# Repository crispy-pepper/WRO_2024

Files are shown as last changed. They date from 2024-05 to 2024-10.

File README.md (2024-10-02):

# SJJ | WRO - Future Engineers | Canada

## Team Members 
- Sunni Xue (right)
- Jayden Li (middle)
- John Weng (left) <br>
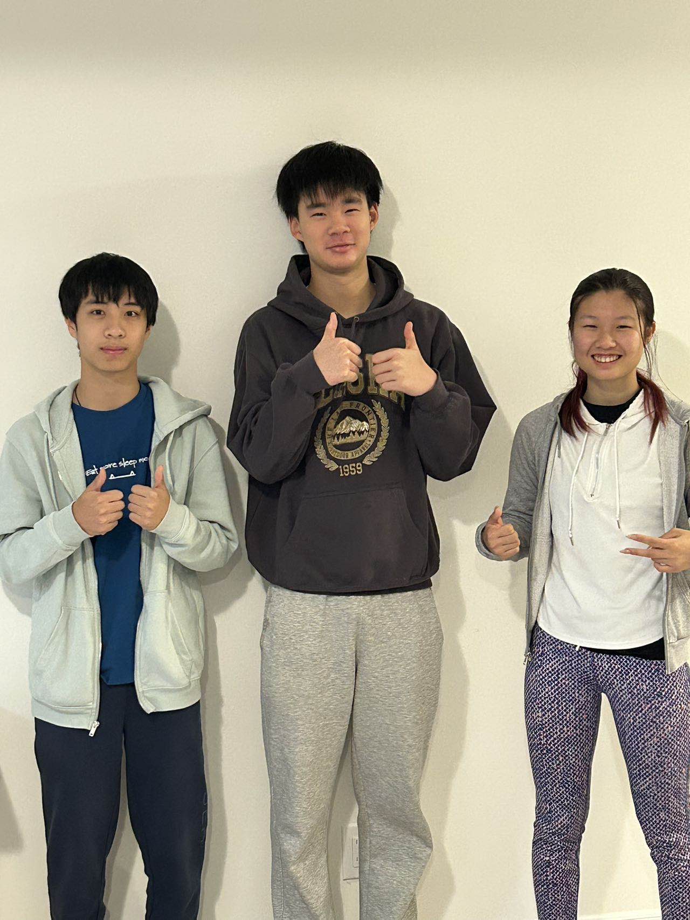
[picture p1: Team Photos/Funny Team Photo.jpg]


## Content 📖📚
 
| Folder  | Content| 
| -- | -- |
| [`Team Photos`](/Team%20Photos)| [Official team photo](/Team%20Photos/Official%20Team%20Photo.jpg), [funny team photo](/Team%20Photos/Funny%20Team%20Photo.jpg) |
| [`Vehicle Photos`](/Vehicle%20Photos) | [Bottom view](/Vehicle%20Photos/bottom.jpg), [front view](/Vehicle%20Photos/front.jpg), [left view](/Vehicle%20Photos/left.jpg), [rear view](/Vehicle%20Photos/rear.jpg), [right view](/Vehicle%20Photos/right.jpg), [top view](/Vehicle%20Photos/top.jpg) |
| [`models`](/models) | [Final base model](/models/base%20v3.stl), [final camera base model](/models/camera%20base.stl), [final camera holder model](/models/camera%20holder%20v5.stl), [expansion board diagram](/models/expansion_board_diagram.png), [final fan holder model](/models/fan%20holder%20v2.stl), [old and unused models (zipped)](/models/old) |
| [`other`](/other) | [Images used in documentation](other/images-used) |
| [`schemes`](/schemes) | [Schematic explanations](/scheme/README.md), [expansion board schematic](/schemes/Raspberry%20Pi%20Expansion%20Board%20Schematic.png), [Raspberry Pi schematic](/schemes/Raspberry%20Pi%20Schematic.png), [vehicle schematic](/schemes/Vehicle%20Schematic.png) |
| [`src`](/src) | [Obstacle challenge final](/src/ObstacleChallenge.py), [open challenge final](/src/OpenChallengeFinal.py), [HSV finder](/src/HSVRange.py), [test files](/src/Tests) |
| [`videos`](/videos) | [Open challenge](/video/README.md), [obstacle challenge](/video/README.md) |

Section  | Content 
--- | --- |
[`Task`](#task) | Introduces the problem/task of this competition
[`Engineering Materials`](#engineering-materials) | Engineering materials used to complete the vehicle 
[`Obstacle Management`](#obstacle-management) | Obstacle Management
[`Movement Considerations`](#movement-considerations) | How and why we chose the specific moving parts used in the vehicle
[`Power Considerations`](#power-considerations) | How and why we chose the battery used with the vehicle
[`Assembly Instructions`](#assembly-instructions) | How to build the vehicle

## Task
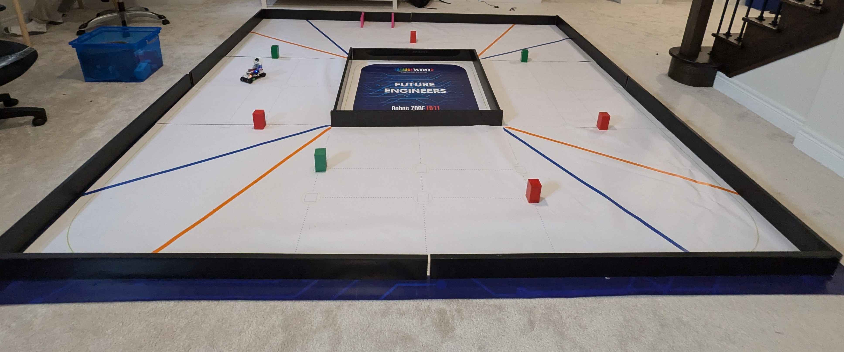
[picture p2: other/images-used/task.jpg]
plot

Obstacle challenge field

### Problem Statement
[The self-driving car challenge in this season is a Time Attack race: there will not be multiple cars at the same time on the track. Instead, one car per attempt will try to achieve the best time by driving several laps fully autonomously. The traffic signs indicate the side of the lane the vehicle has to follow.](https://www.wro2022.org/theme/future-engineers)

In order to perform the race, the car must drive three laps. The vehicle is not allowed to move or knock down the traffic signs.

**GOAL: Build a self-driving, autonomous vehicle that completes 2 challenges: the open challenge and the obstacle challenge.** 
### Open Challenge
The open challenge is where the car must complete three full laps around the field without touching a wall. The size of each side of the field is determined by random chance of either 100 cm or 60 cm. The direction in which the car drives is also randomized. 
 
### Obstacle Challenge
The obstacle challenge is where the car must complete three full laps around the field, avoiding different coloured traffic signs (pillars). If the pillar is red, traverse on the right side; if the pillar is green, traverse on the left. The direction in which the car drives is randomized. After the third lap, depending on the last pillar, the car must continue in the same direction or change directions to find the parking lot. The car must then back into the parking lot without touching either of the ends. The size of each side of the field remains constant, 1 metre for each side. 

## Engineering materials
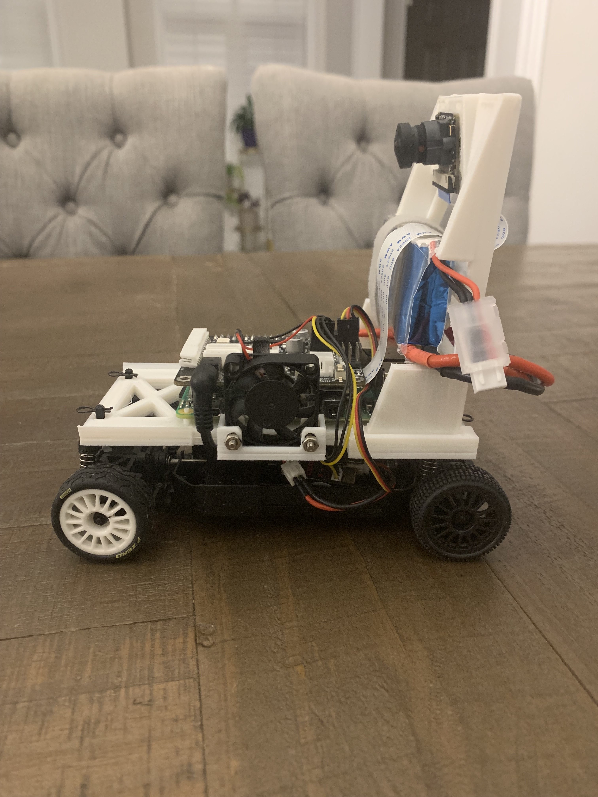
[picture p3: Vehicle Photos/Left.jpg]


### Car Base
* [Carisma 80468 GT24RS 1/24 4WD On-Road Brushless RTR Retro Rally Car as the structure](https://www.ebay.ca/itm/134622499234)
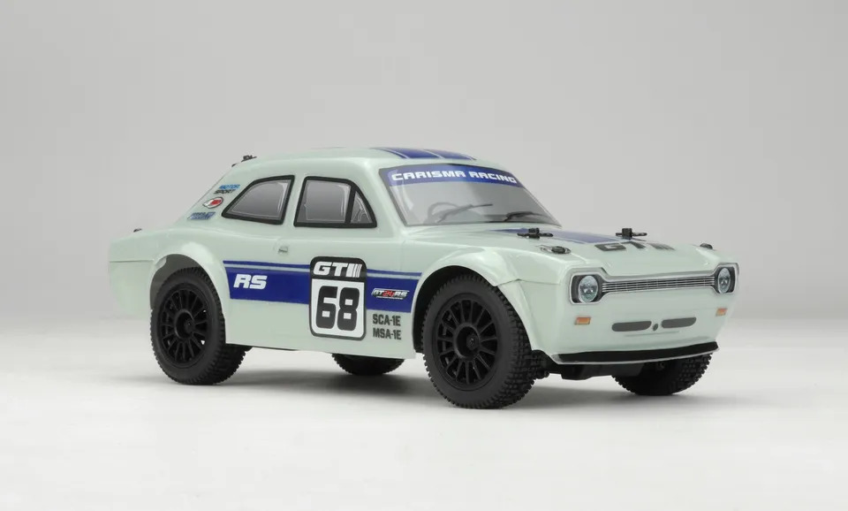
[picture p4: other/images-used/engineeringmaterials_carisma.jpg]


* Carisma 2022 Ford PUMA Hybrid Rally 1 M-Sport 4WD 1/24 Scale RTR 1 87868 as steering system of the car
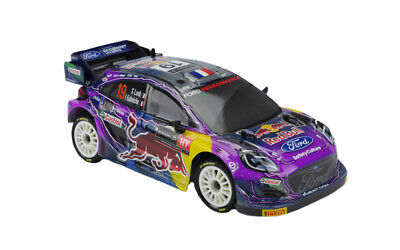
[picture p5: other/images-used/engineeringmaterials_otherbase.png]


* [Furitek Micro Komodo 1212 3450KV Brushless Motor](https://furitek.com/products/furitek-micro-komodo-1212-3456kv-brushless-motor-with-15t-steel-pinion-for-fury-wagon-fx118)
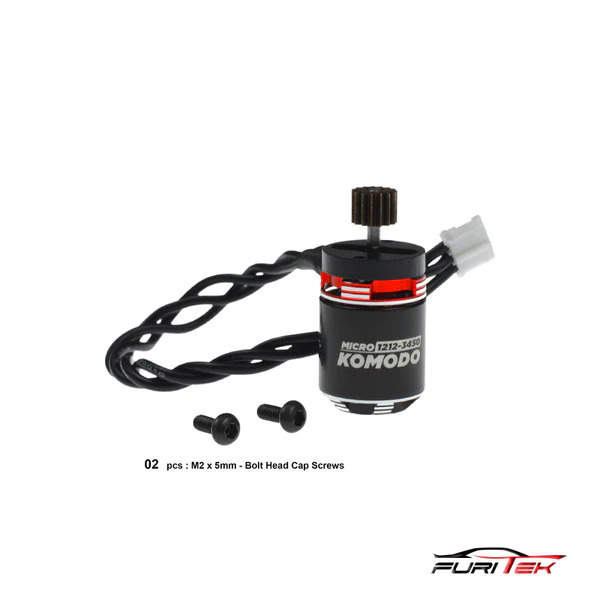
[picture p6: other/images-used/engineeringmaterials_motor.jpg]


* [Furiteck Lizard Pro 30A/50A Brushless ESC](https://furitek.com/products/combo-of-furitek-lizard-pro-30a-50a-brushed-brushless-esc-for-axial-scx24-with-bluetooth)
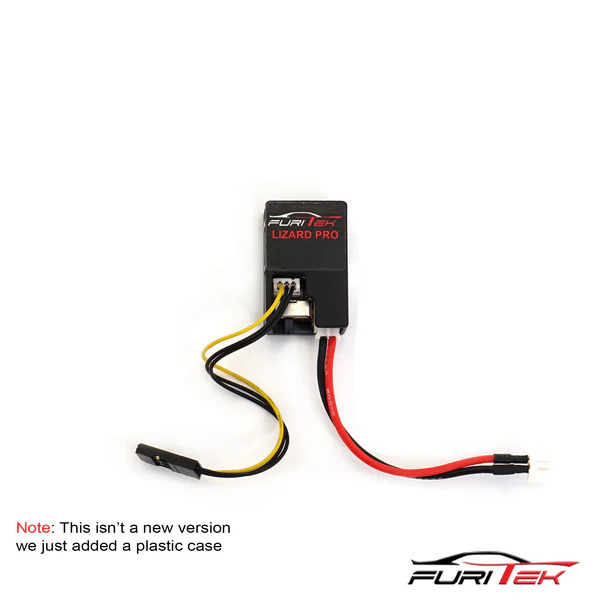
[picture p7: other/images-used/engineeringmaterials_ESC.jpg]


* [Hitec HS-5055MG Servo](https://ca.robotshop.com/products/hs-5055mg-metal-gear-micro-servo-motor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)
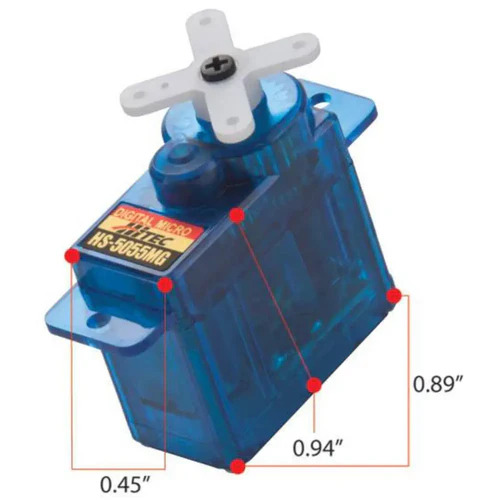
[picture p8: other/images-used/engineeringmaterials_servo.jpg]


* [Gens Ace 2S1P 1300mAh 7.4V battery](https://www.adrenalinehobby.com/products/gens-ace-g-tech-1300mah-2s-7-4v-25c-lipo-deans-plug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)
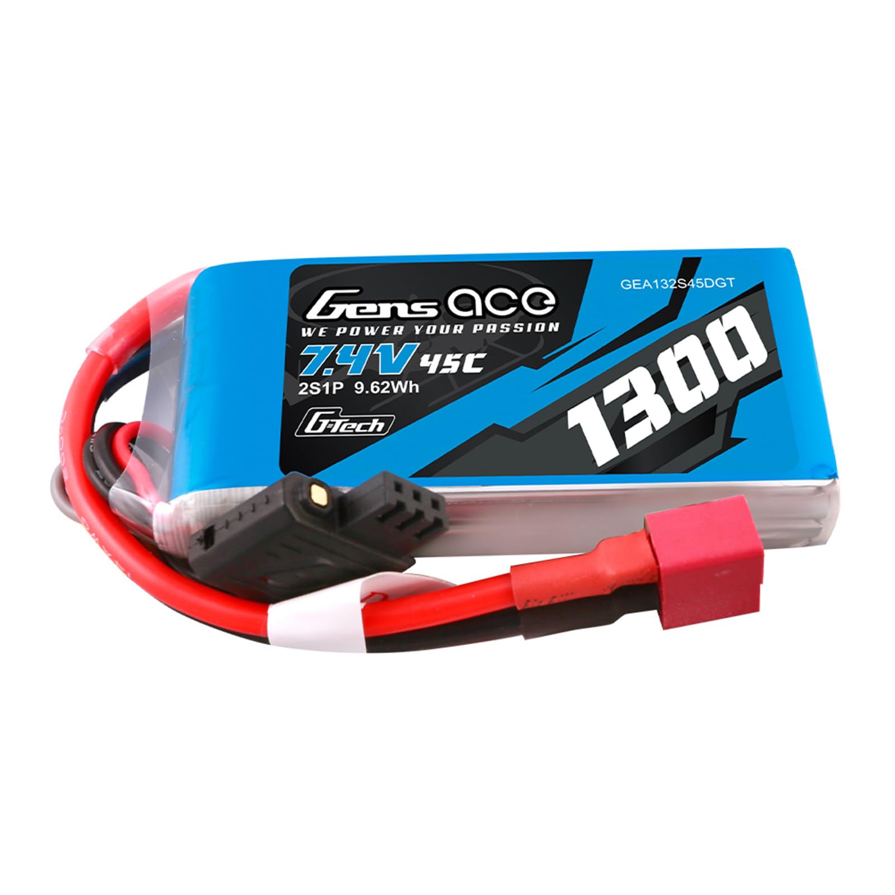
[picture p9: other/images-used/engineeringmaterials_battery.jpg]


* Rasberry PI 4 Model B
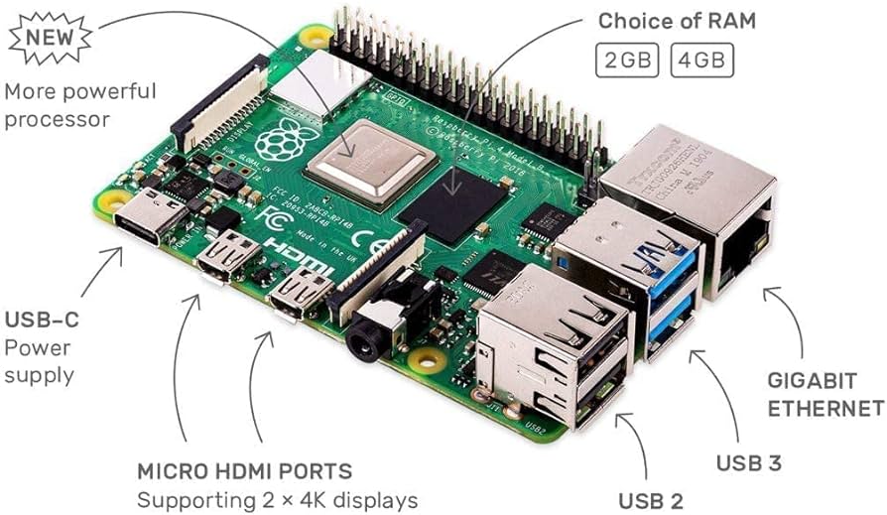
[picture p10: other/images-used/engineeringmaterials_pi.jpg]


* [Raspberry Pi 5 Expansion Board Model A(DC Port)](https://www.hiwonder.com/collections/expansion-board/products/expansion-board-for-raspberry-pi-5)

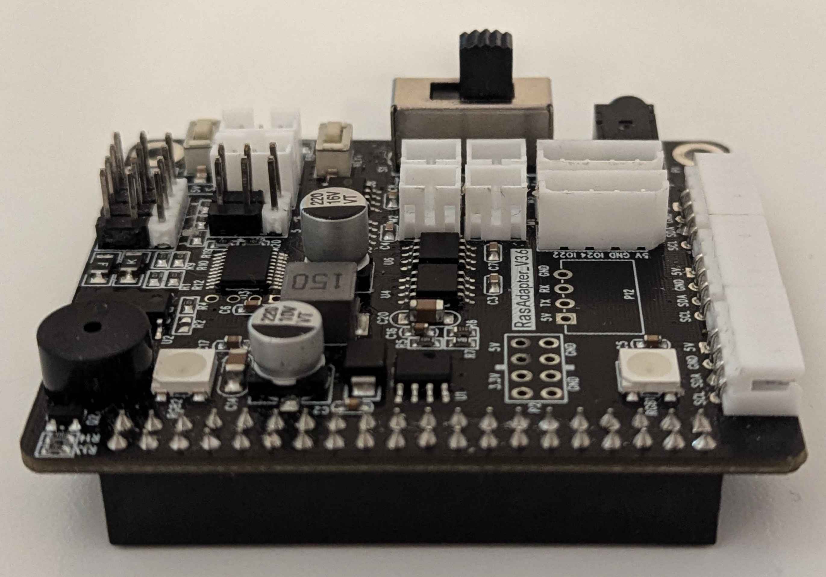
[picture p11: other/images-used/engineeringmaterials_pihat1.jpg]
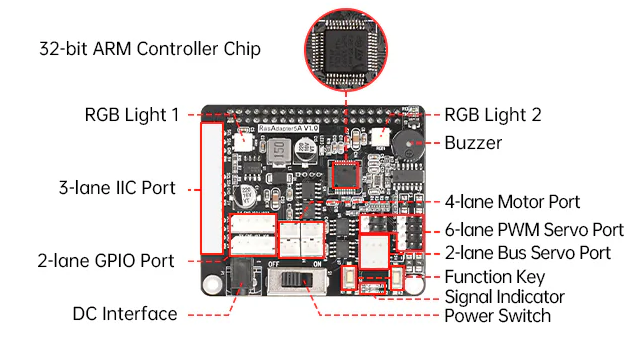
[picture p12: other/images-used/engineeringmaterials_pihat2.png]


* Mini Rocker Switch
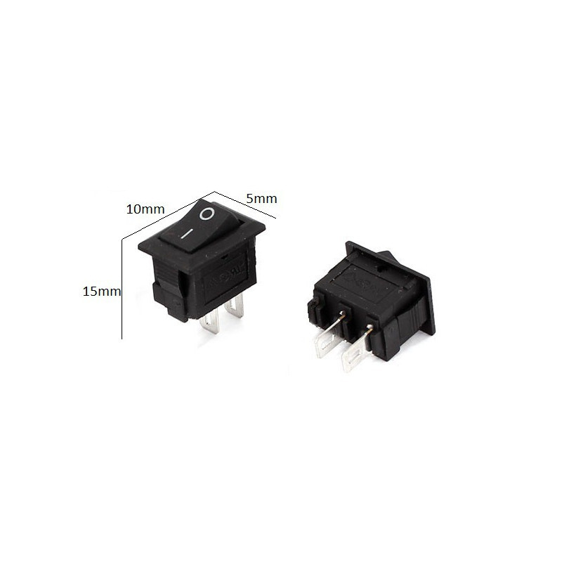
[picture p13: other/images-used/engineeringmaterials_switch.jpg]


* 5V Mini Fan
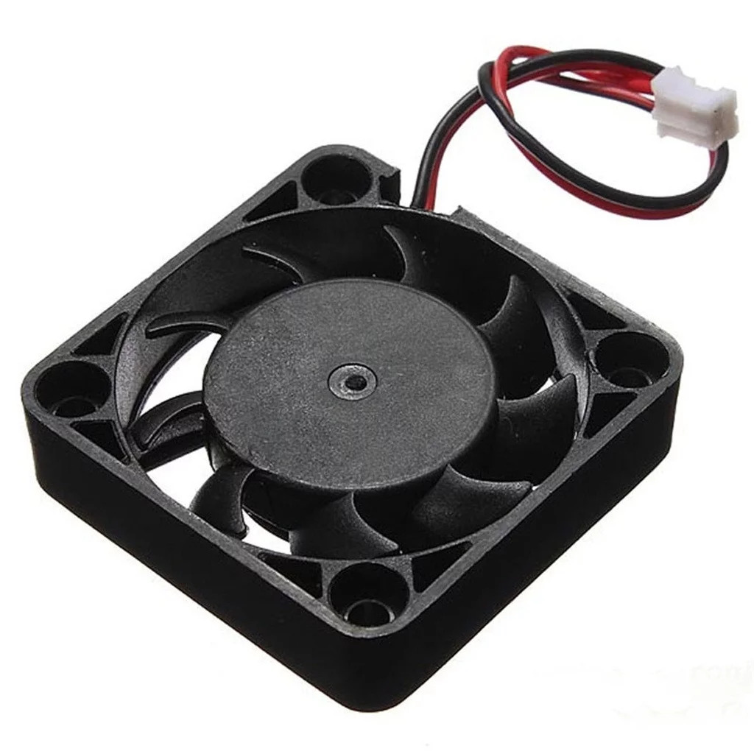
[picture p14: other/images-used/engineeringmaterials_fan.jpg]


* [3D printed base](/models)
* MicroSD card

### Sensors

* [SainSmart Camera Module RPi3, 5MP, Fish-Eye](https://www.sainsmart.com/products/noir-wide-angle-fov160-5-megapixel-camera-module)
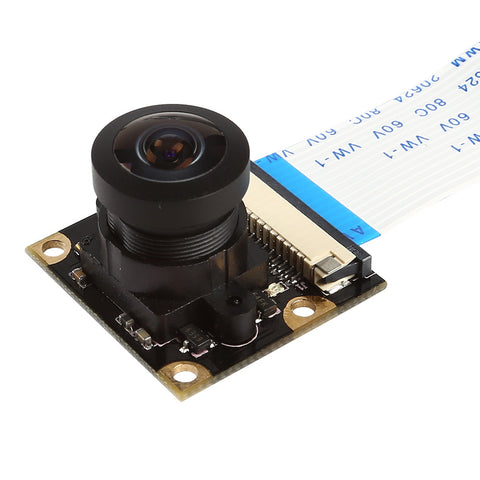
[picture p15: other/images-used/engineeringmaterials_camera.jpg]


## Obstacle Management
**ss of cv2 window**

- **Libraries Used** - `math` - `sys` - `cv2` - `numpy` - `time` - `picamera2` - `HiwonderSDK.Board` - `libcamera`

#### Wall-Following/Track Centering

Our open and obstacle challenge used the same wall following algorithm that guaranteed the robot to remain in the center of the two walls when needed. To make sure that laps stayed consistent and the vehicle did not touch the walls, we had to implement some form of track centering. We did this using a [SainSmart Camera Module RPi3, 5MP, Fish-Eye](#engineering-materials). With the mounted camera, we were able to capture the surroundings of the vehicle frame by frame. 

Using these captures, we applied four (left top, left bottom, right top, right bottom) unique ROIs (regions of interest) that captured the areas of the walls diagonally ahead on both sides. We then created a black threshold mask to calculate how much area of the ROIs was black. Using these areas, we could determine if the vehicle is veering too far to one side by calculating the difference between the two sides and adjust the robot accordingly. To physically implement this calculation, we used a Proportional-Derivative (PD) algorithm approach, deciding that a combining the two factors would be perfect for our goal of following the walls.

```py
error = left_area - right_area
turn (error)(proportional gain) + (change in error value over time)(derivative gain)
```

This algorithm calculates the precise angle the servo should turn by taking the difference between the two sides multiplied it by the proportional value (constant) and adding it to the derivative value (constant) multiplied by the difference between the current and last difference in the two sides. The use of PID control allows stable turning with less oscillating and overcorrection, ensuring that the vehicle remains centered on the track.

### Open Challenge

#### Turning
Our initial turning algorithm was simple in premise: when one of the walls was no longer detected, the robot would turn that direction. In practice, this algorithm performed inadequately because when turning into a narrow section, the robot would not turn at a great enough angle and therefore veer too close to the wall.

```py
if left_area is none
	turn sharp left until left_area is detected
else if right_area is none
	turn sharp right until right_area is detected
```

Realizing that waiting for the wall to be passed would not provide an adequate turn, our goal was to create a turn algorithm that could pre-emptively detect that a turn was needed. Our solution was to use the blue and orange lines on the mat to decide when to turn. Another small ROI was added to detect orange and blue contours. 

Depending on which of the colours was detected first, the algorithm would turn the correct direction accordingly. The turn would be ended after the opposite colour line was detected and the respective wall was detected again on the camera.

The same logic for if a wall was no longer detected from the first algorithm was also used in conjunction, creating an algorithm that would turn in a more optimized path. 

```py
if orange line detected
	turn sharp right until blue line detected
	
else if blue line detected
	turn sharp left until orange line detected
	
if left_area is none
	turn sharp left until left_area is detected
else if right_area is none
	turn sharp right until right_area is detected
```

This algorithm performed much better, but had a flaw: the line would be detected and the turn would start, but once the orange line was detected again, the turn would end. Therefore, we created a solution that would allow for the wall to fully be passed before ending the turn. This solution was adding a short timer to the turn that would ensure that the turn was not ended early.

```py
if orange line detected
	turn sharp right until blue line detected
	
	if blue line detected
		increment turn_timer
		
	if turn_timer greater than turn time
		end the turn
	
else if blue line detected
	turn sharp left until orange line detected
	
	if orange line detected
		increment turn_timer
	
	if turn_timer greater than turn time
		end the turn
		
if left_area is none
	turn sharp left until left_area is detected
	
else if right_area is none
	turn sharp right until right_area is detected
```

This algorithm was both reliable and efficient, allowing the robot to travel at high speeds with no risk of hitting the walls. 

### Obstacle Challenge

#### Turning
Similar to how we centered the vehicle, we also used the area of black in the ROIs to decide when to turn. If one ROI's black area was less than a certain value, it would mean that the wall has disappeared and the servo would turn to the most extreme angle. The vehicle would keep turning until the wall appeared again. This naïve approach was straightforward but failed in many cases because of the pillar-avoidance requirement:

```py
if left_area is none
	turn sharp left until left_area is detected
else if right_area is none
	turn sharp right until right_area is detected
```

However, this did not always work because pillars would make the robot move into unexpected areas. To fix this, we added another trigger for the turning sequence: the lines on the mat. This algorithm was very similar to the line detection in the open challenge without the timed aspect later added to that algorithm. 

```py
if orange line detected
	turn sharp right until blue line detected
	if right_area is detected
		stop turning
	
if blue line detected
	turn sharp left until orange line detected
	if left area is detected 
		stop turning
```

If a pillar was detected in the turn, the turn would be ended when the pillar is on the correct side of the screen. For example, when turning left into a green pillar, the turn would be ended when the green pillar is on the right side of the screen. This ensures that the turn allows the robot to travel into the next straight section while passing pillars on the correct side. 

#### Pillar Maneuvering

The camera scans for pillars using another ROI that encapsulates the center of the camera view and a red and green colour mask. The algorithm would find the closest pillar by finding the largest contour. Depending on the colour of this contour, we could decide whether to go left or right. We started with a naïve approach of turning a constant amount left or right when the pillar was detected.

##### Pillar Maneuvering: 
The camera scans for pillars using another ROI that encapsulates the center of the camera view and a red and green colour mask. The algorithm would find the closest pillar by finding the largest contour. Depending on the colour of this contour, we could decide whether to go left or right. We started with a naïve approach of turning a constant amount left or right when the pillar was detected.

```py
if red_area greater than pillar_threshold
	turn right
else if green_area greater than pillar_threshold
	turn left
```

However, this posed many challenges with overturning, underturning, turning past before it got to the pillar, and not turning at all. We fixed this by adding a constant target value for both coloured pillars and adjusting according to the distance between the pillar's left x-value and the target line. The vehicle would constantly try to match the x-value up with the target line. This way, the vehicle would know to continue turning towards the pillar or to turn the other way to correct the overturning. Additionally, we found that it would be beneficial for the robot to turn at a greater angle if the pillar is closer to avoid the pillar in urgent situations. Therefore, we added another factor into our turn degree: y-axis gain. This functionality would turn the servo motor at a greater angle based on the y-coordinate of the pillar, which is the straight distance forward from the robot. 

```py
if red_area greater than pillar_threshold
	error = target - red_pillar_x
	turn (error)(pillar proportional gain) 
	+ (change in error value over time)(pillar derivative gain)
	+ (y axis gain)(red_pillar_y)
	
```

#### Backtracking: 
Because there was a limitation to how many degrees our vehicle could turn at a time, there was an issue of not turning enough in time. To solve this, we would check how big the current pillar was and calculate if the vehicle would make it past successfully (without touching or moving anything). If the vehicle could not, it would backtrack at the opposite angle, readjust, and continue forward. This would continue until the vehicle could successfully make it past.

```py
if pillar_area greater than avoidable distance and pillar_x is not on the correct side:
	reverse the robot
```

#### 3-Point Turn

The three point turn algorithm is required when the last pillar of the second lap is red. This signals that the robot must complete the final lap in the opposite direction. A three point turn is required to change the orientation of the robot. The algorithm is simple and effective. If the three point turn is needed, the robot will turn sharply right until a wall is seen. This allows the robot to achieve the maximum angle from one turn. Once a wall is detected in front of the robot, the second phase of the turn will be activated and the servo will turn to a sharp left angle and reverse the robot. Finally, the robot turns at a sharp right angle and goes forward, ending in the opposite orientation from where it started. This allows the robot to complete the last lap in the appropriate direction.

```py
three point turn
	turn sharp right 
	go forward
	if wall is directly in front of robot
		turn sharp left
		reverse the robot
		turn sharp right
		go forward
		end the three point turn
	repeat
		
if last pillar is red
	go past the pillar
	start three point turn
```

#### Parking
After finishing the three laps, the vehicle must park find and stop inside the magenta parking lot. Rather than parallel parking, we decided to go head first, directly turning into the allotted space. This was because when first reading the problem, we found that as long as the vehicle was fully inside the boundaries of the parking lot, the orientation did not matter to achieve full marks. This is also the main driving factor behind why we chose a small chassis (< 20 cm because the width of the parking lot is 20 cm).

The parking algorithm works by first circling the field on the outside of all pillars (as it does not need to abide by the traffic rules after the completion of the third lap) until it detects a large enough magenta contour to initiate the parking sequence. This condition is calculated by finding the largest magenta contour in the left and right ROIs and the y-coordinates of their bounding rectangles and comparing them to predetermined constants. If both the y-coordinate and size conditions are met, the vehicle is in the correct position to start parking. Depending on the size of the maximum left and right magenta contour, the side the parking lot is located on can be deduced. 

```py
if rightY/leftY is greater than a value and maxAreaRight/maxAreaLeft is greater than a value
	if not currently parking on the left or right side:
		initiate parking on the left/right side
		go forwards slower
                created new, bigger center ROI
```

The parking sequence works by directly turning into the parking lot forward and backing out in the same direction if needed; repeated until the area in front of the vehicle is larger than a value. It knows when to back out by checking if the center y-coordinate of the largest contour's bounding rectangle (centerY) is greater than a certain, meaning the vehicle will hit the wall if it continues forward.

```py
if currently parking on the left or right side
	if centerY is greater than a value:
		stop
		turn the servo to the maximum in the correct direction
		go backwards
		stop

	else
		turn the servo to the maximum in the correct direction
		go forwards
```

Once the area of the wall in front of the vehicle is large enough, it will continue straight forward to be sure the vehicle is fully in, stop, and exit the main loop.

```py
 if area in front is greater than a value:
	turn servo straight
	go forwards
	stop and exit
```

## Movement Considerations
* Servo for steering
* Motor for FWD (four-wheel drive)
* The vehicle [Chassis is a Carisma 80468 GT24RS 1/24](#engineering-materials) so the vehicle is small enough to fit in the parallel parking space vertically
* The components are mounted on a 3d printed base sitting on top of the chassis, with the motor and servo being mounted directly into the chassis
* The [Furitek Micro Komodo 1212 3450KV Brushless Motor](#engineering-materials) was chosen combined with a [Furiteck Lizard Pro 30A/50A Brushless ESC](#engineering-materials) because brushless motors are mechanically driven, which allows more precise speed controls, longer life and higher efficiency with less maintenance.
* The servo was chosen because.. (use engineering principles: speed, torque, power etc) <br>


In both the open and obstacle challenge, vehicle movement is essential for ensuring optimal performance. The vehicle is managed through a four-wheel drive configuration, with front-wheel steering. This configuration resembles everyday cars on the street, and allows for movement forwards and backwards, as well as turning in both directions. 

For the propulsion of the vehicle, we choose the [Furitek Micro Komodo 1212 3450KV Brushless Motor](#engineering-materials) due to the high speeds that the motor can achieve, indicated by the 3450KV rating. High speeds allow rapid movements and give us headroom without needing to max out the motor while running. Brushless motors are known for providing consistent torque which allows the vehicle to move smoothly. Brushless motors are electrically driven, which allows more precise speed control, and have a longer lifespan with less maintenance, which is ideal for our vehicle. We paired the motor with a [Furiteck Lizard Pro 30A/50A Brushless ESC](#engineering-materials), which regulates the power delivered to the motor, allowing for smooth acceleration and deceleration and ensures the safety and consistency of the motor.

We chose the [Hitec HS-5055MG Servo](#engineering-materials) for our steering capabilities. It is perfect for small vehicles, with high torque at 1.2kg/cm at 4.8V or 1.5kg/cm at 6V. This allows the turning capabilities of the car to be consistent due to the strength of the servo and ensures the vehicle can turn quickly and accurately at low speeds or when stationary, which is essential for this competition. 

The vehicle is based on the [Charisma 80468 GT24RS 1/24 model](#engineering-materials), which was selected due to its compact size, which allows the vehicle to parallel park vertically, making the job much easier. The small size also contributes to the overall agility of the vehicle, making it easier to maneuver in tight spaces. 

The motor and servo replace the original components in the [Charisma 80468 GT24RS 1/24 model](#engineering-materials), with the servo needing modifications to the chassis of the car. The other components of the car are attached through a 3d printed base that is clipped in on top of the car. <br>

However, our chassis still had one major problem; the max turning degree of the front-wheel steering was less than 30 degrees. This became a major issue later on as with such a large turning radius, the vehicle could not possibly move agilely in difficult pillar configurations. After WRO Canada, we switched out the front-wheel steering area for a different chassis’s front-wheel steering. This new steering piece came from the [Carisma 87868 Ford PUMA Hybrid Rally 1/14](#engineering-materials) This was because we found that through testing, a different front-wheel steering part paired with the same base chassis would result in a higher max turn degree.

## Power Considerations
* Sensors and power management
* Reference schematic 


The power and sensor systems are critical to the vehicle's performance in navigating the challenges of the competition. For this project, the vehicle is powered by a [Gens Ace 2S1P 1300mAh 7.4V battery](#engineering-materials). This battery has a discharge rating of 45C, meaning it can provide up to 58.5 Amps of current, which is more than enough to meet the power requirement of the vehicle's components.

The battery serves as the power source for the vehicle, providing energy for all parts. The [Furitek Lizard Pro 30A/50A Brushless ESC](#engineering-materials) is connected to the battery to regulate the power delivered to the [Furitek Micro Komodo 1212 3450KV Brushless Motor](#engineering-materials). This ESC is required to ensure smooth acceleration and deceleration, protecting the motor from potential damage due to power surges.

The Raspberry Pi, which acts as the vehicle's brain, has a power consumption of 1280mA under heavy stress, shown by studies. Given the battery's capabilities, this power draw is much less than what the battery can provide, allowing the Raspberry Pi to operate properly while managing all sensor inputs and processing.

The vehicle's sensing capabilities include a [SainSmart Camera Module RPi3](#engineering-materials), which is used in both the open and obstacle challenges. The camera is equipped with a fish-eye lens, offering a wider field of view. This visual range enables the vehicle to detect obstacles, such as walls and pillars, and to more effectively process the surroundings. 

In the obstacle challenge, the camera detects the walls, the colour of the pillars, the parking space, and the lines on the course. The vehicle uses this information to change the direction left or right accordingly, ensuring it stays on course. The fish-eye lens enhances the vehicle’s ability to capture more of the field at closer distances, providing the system with more information to make timely decisions.

<br><br><br>

## Assembly Instructions
### Software
**1. Raspberry Pi OS**
 - Download and install the official Raspberry Pi Imager from [https://www.raspberrypi.com/software/]

**2. Turbo Pi**
 - Using Raspberry Pi Imager, copy the TurboPi operating system onto a microSD card
 - Insert into the Raspberry Pi
   
**3. Connecting to the Raspberry Pi**
   - Download and install RealVNC from [https://www.realvnc.com/en/connect/download/viewer/]
   - Plug in the Raspberry and wait until wifi access point “HW-xxxxxx” shows up in your wifi list
   - Launch RealVNC and create a new connection with server `192.168.149.1`
       - Username: pi
       - Password: raspberry
   - 
**3. Auto-running the program on start**
  - Transfer OpenChallengeFinal.py/ObstacleChallengeFinal.py onto the Raspberry Pi and open command prompt
  - Open command prompt and run `sudo nano /etc/rc.local`
  - Add the line `sudo bash -c 'sudo python3 /home/pi/<<directory>>/<<filename.py>>' &` before the line `exit 0` and save and close
  - Reboot the Raspberry Pi and the program should automatically run on start
   
<br><br>
### Hardware
**1. Disassembling the Chassis:**
 - Begin by unscrewing the cover of the Carisma 80468 GT24RS 1/24 chassis. This includes removing the top pole that supports the rear of the cover.
 - Next, unscrew the top shell of the vehicle. After the shell is removed, detach the components securing the servo and motor in place.

**2. Creating Space for New Components:**
 - Remove the battery holder from the chassis, followed by the front partition of the servo holder. This step creates sufficient space for the 
installation of the new motor and servo.

**3. Installing the New Motor:**
 - Replace the original motor with the Furitek Micro Komodo 1212 3450KV Brushless Motor, using the original motor compartment and holder.

**4. Installing the New Servo:**
 - Replace the original servo with the Hitec HS-5055MG Servo. Screw a long screw into the servo horn/arm so that it moves the steering mechanism. 
 - Make sure to clip the standoffs of the servo to fit into the chassis.

**5. Wiring the Power System:**
 - Connect the Gens Ace 2S1P 1300mAh 7.4V battery cable to the Furiteck Lizard Pro 30A/50A Brushless ESC cable. To ensure proper power delivery to the motor and other components, follow the wiring provided in the [README](/schemes/README.md) of the schemes folder

**6. 3D Printed Components Installation:**
 - Print a [base](/models/base%20v3.stl) and a [camera holder](/models/camera%20holder%20v6.stl) using a 3D printer.
 - Install the camera holder into the base by aligning it with the inset negatives on the base.
 - Mount the assembled base onto the poles that originally supported the vehicle’s cover, ensuring the camera holder is positioned over the rear wheels. Use the original pins from the car to securely clip the base in place.

**7. Installing the Camera:**
 - Secure the camera into the holder using screws, aligning it with the holes in the camera holder. Ensure the camera is firmly fixed to prevent any movement during operation.

**8. Mounting the Battery:**
 - Place the battery into the  cutout within the camera holder's supports. Use tape, Velcro, or zip ties to secure the battery in place, ensuring it remains stable during vehicle operation.

**9. Installing the Raspberry Pi:**
 - Place the Raspberry Pi on top of the base, ensuring that the pins on the base align with the screw holes on the Raspberry Pi.

**10. Wiring the Vehicle:**
 - Wire the car together according to the provided schematic, ensuring all connections are secure and correctly aligned. Pay attention to wire management to prevent tangling or obstruction of moving parts or obstruction of the camera.

**11. Final Checks:**
 - Ensure all components are secure and that there is no excess movement. Double-check all wiring connections for correctness and stability.

**12. Running the Code:**
 - Once the assembly is complete, upload the control code to the Raspberry Pi. Check all systems are working by performing a series of tests that can be found in the tests folder located in the src folder.

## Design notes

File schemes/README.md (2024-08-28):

# Electromechanical diagrams

Our vehicle's schematic can be separated into 3 main areas: the power area, [the Raspberry Pi] area(#engineering-materials), and the [Pi expansion board] area(#engineering-materials). <br><br>
****As the Raspberry Pi and expansion board are not of our design, you can find their documentation on their respective sites**
<br>

## The Power Area
The power area contains the [main switch](#engineering-materials), [motor](#engineering-materials) and [motor ESC](#engineering-materials), and [battery](#engineering-materials).  Mandated by the rules, the main switch controls all power flowing through the vehicle. The switch is in series with the battery, which is connected to the Pi expansion board and motor ESC in parallel. Here is what the wiring would look like:<br>
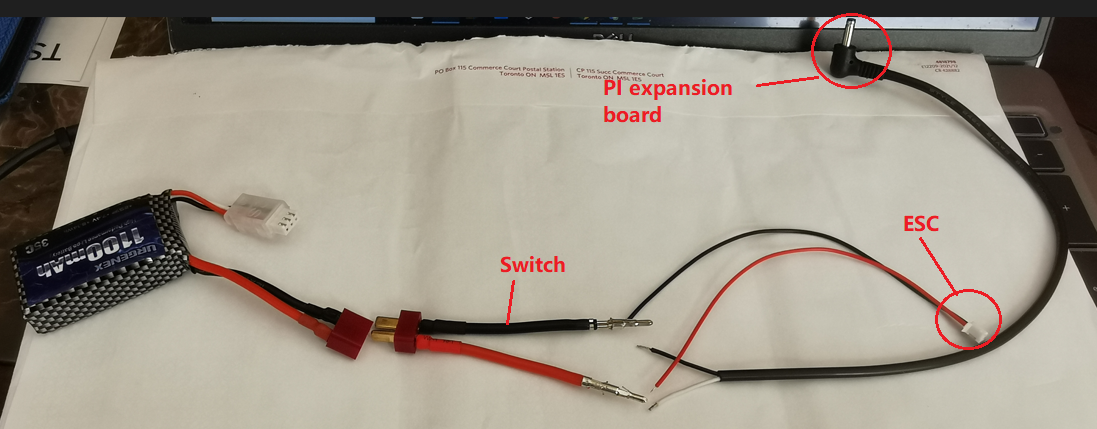
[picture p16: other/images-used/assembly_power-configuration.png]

<br><br>
## The Raspberry Pi Area
The Raspberry Pi Area contains the [camera](#engineering-materials) and [Raspberry Pi](#engineering-materials). The [Raspberry Pi](#engineering-materials) takes in the data from the [camera](#engineering-materials), calculates the outputs, and then sends the outputs to the correct movement instructions to the [expansion board](#engineering-materials) through the 24 connected pins.
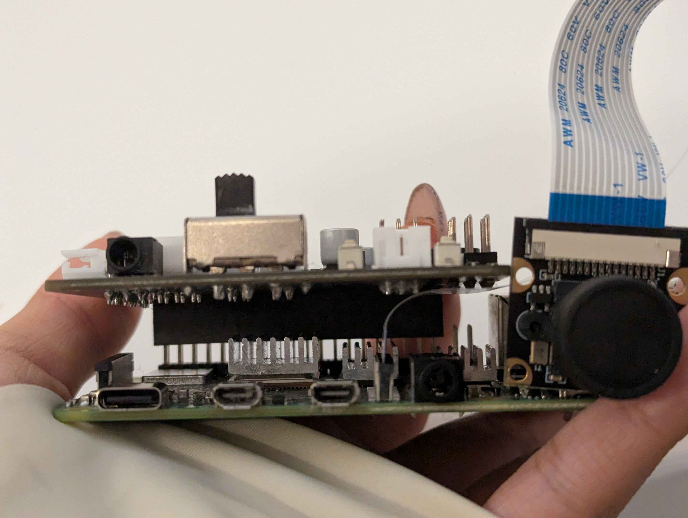
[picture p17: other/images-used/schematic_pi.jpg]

<br><br>
## The Expansion Board Area
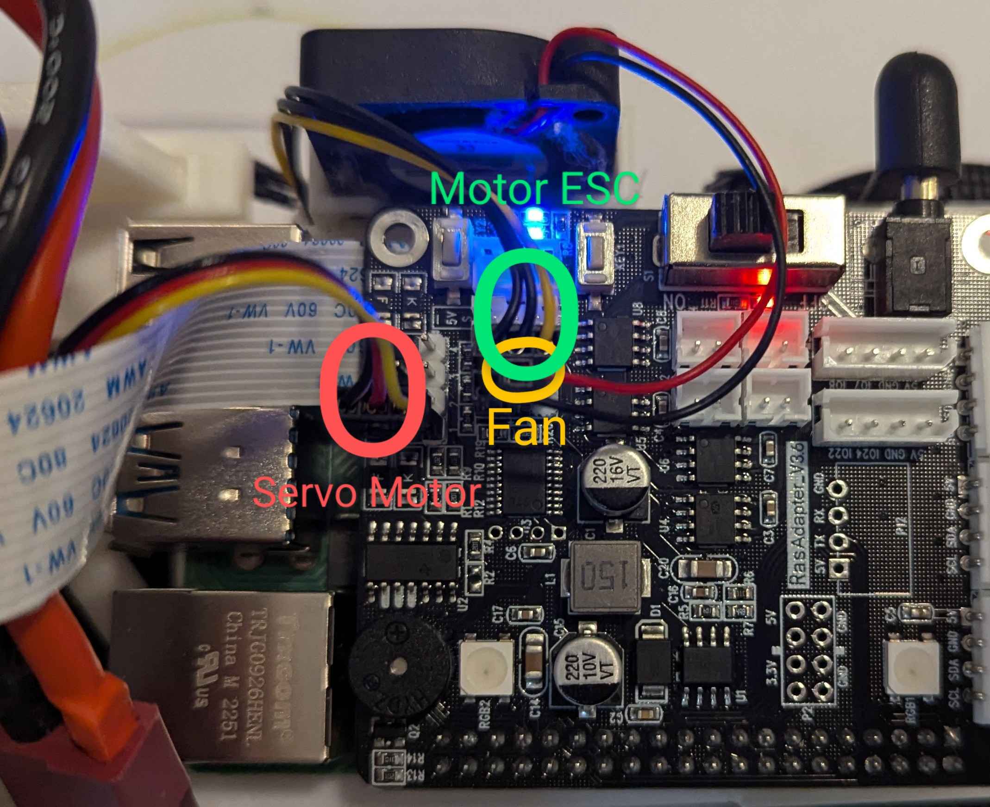
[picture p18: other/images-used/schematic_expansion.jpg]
The expansion board area receives and distributes power, and controls the movement of parts. It is connected to the [switch](#engineering-materials) + [battery](#engineering-materials) (DC Port), the [Raspberry Pi](#engineering-materials) (24 pins), the [motor ESC](#engineering-materials) (5V, ground, PWM [white]), the [servo motor](#engineering-materials) (5V, ground, PWM [white]), and the [fan](#engineering-materials) (5V, ground). It receives instructions through the 24 pin holes connected to the [Raspberry Pi](#engineering-materials) and sends them to the [motors](#engineering-materials).

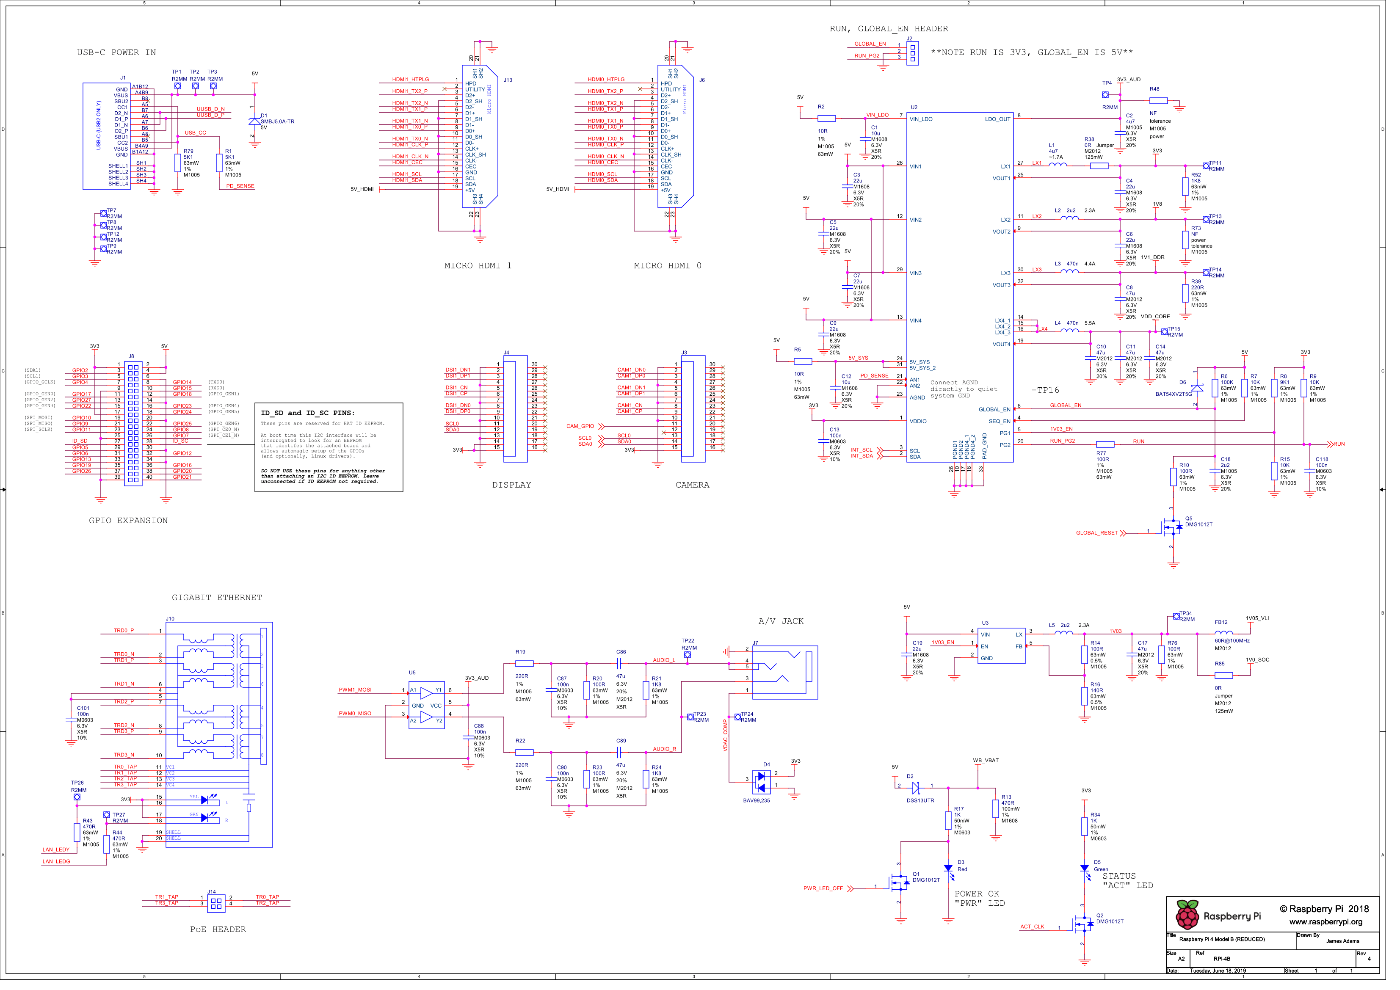
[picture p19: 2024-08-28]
schemes/Raspberry Pi Schematic.png

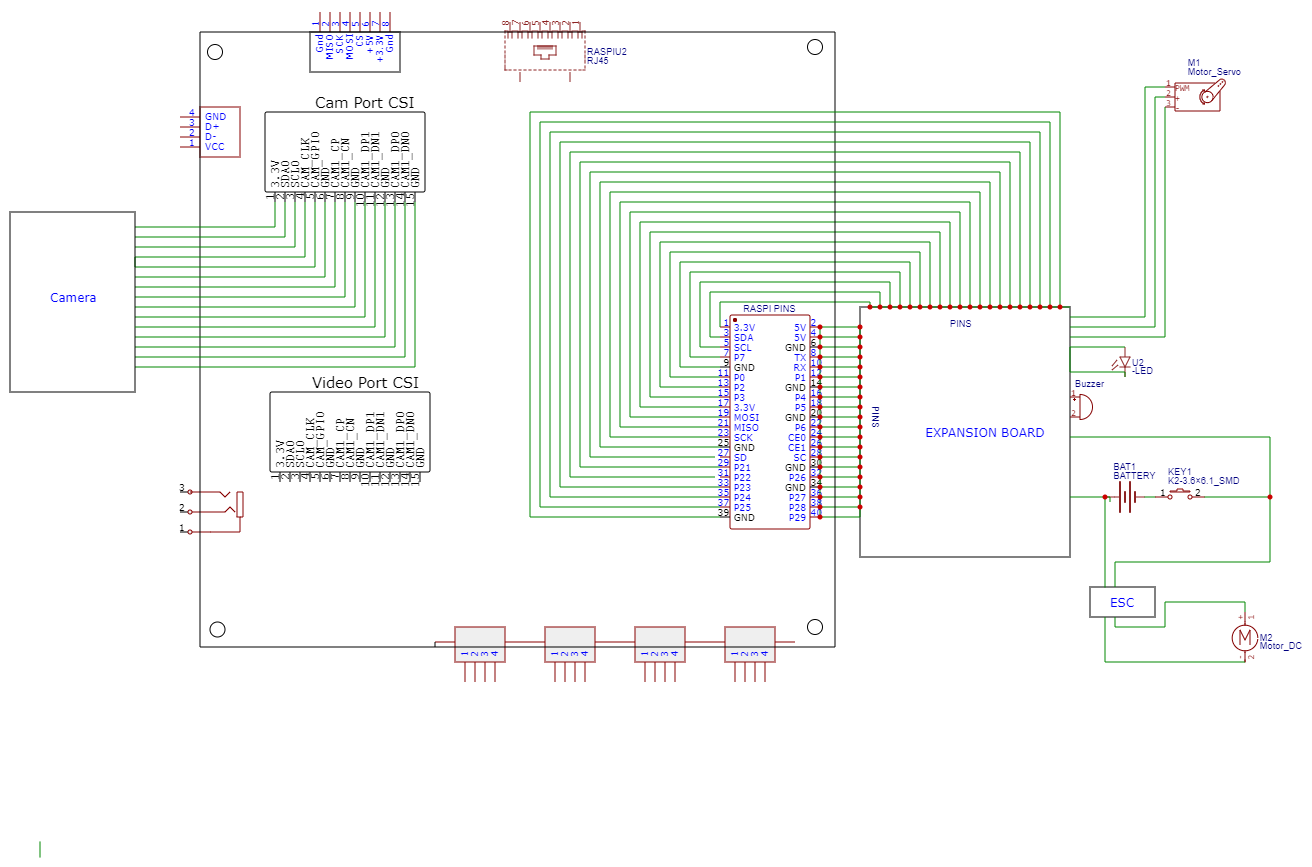
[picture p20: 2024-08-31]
schemes/Full Vehicle Schematic.png

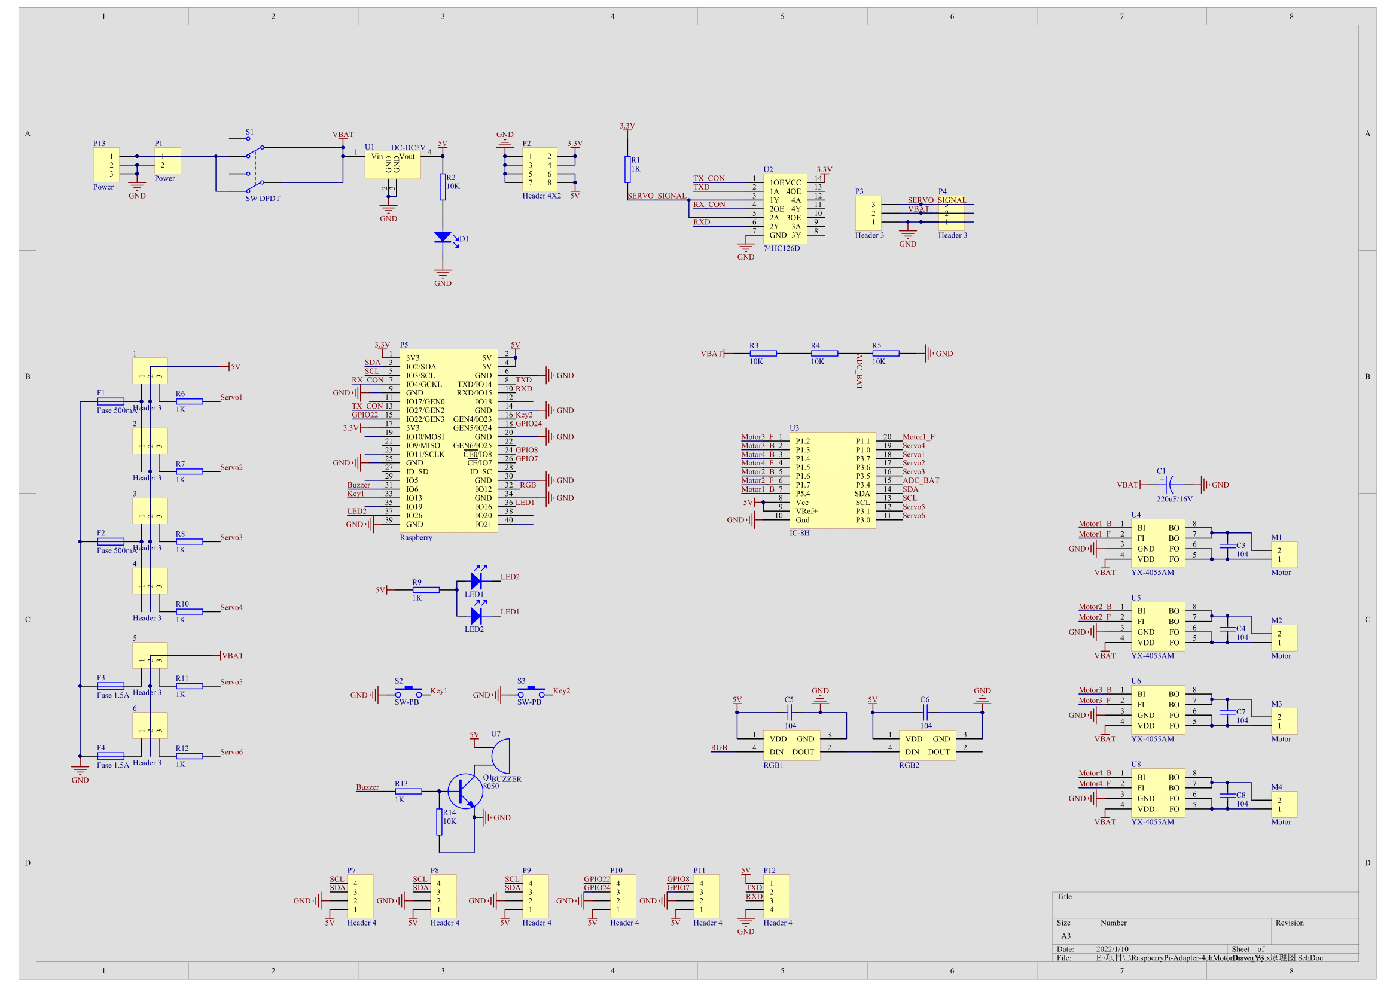
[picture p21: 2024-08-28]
schemes/Raspberry Pi Expansion Board Schematic.png

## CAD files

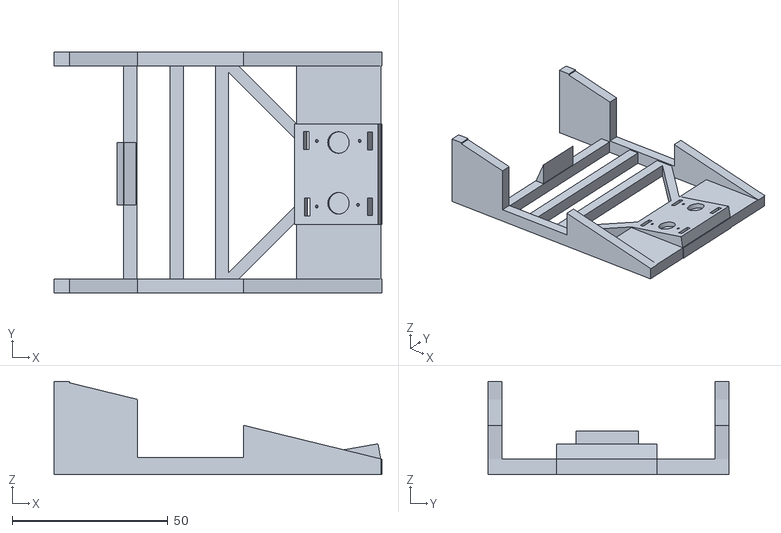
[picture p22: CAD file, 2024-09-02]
models/camera holder v6.stl
105.2 x 77.2 x 30.0

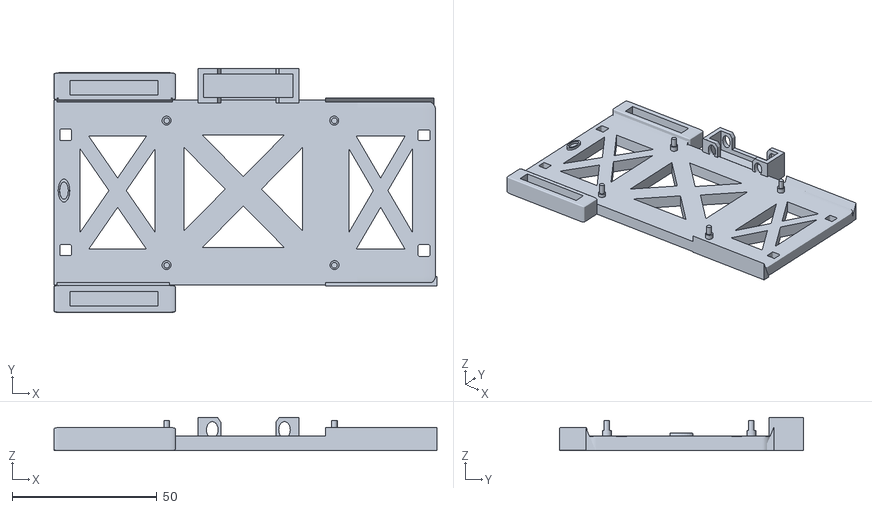
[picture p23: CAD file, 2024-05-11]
models/base v3.stl
132.5 x 84.5 x 11.5

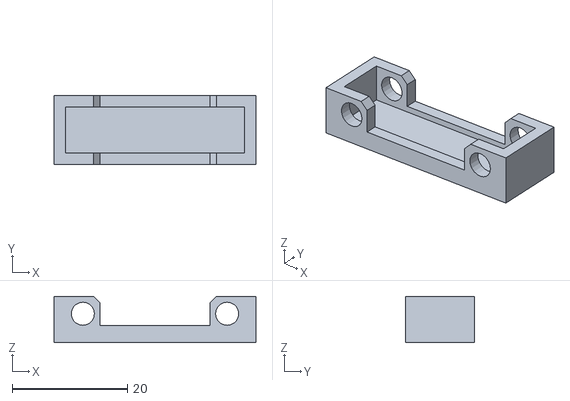
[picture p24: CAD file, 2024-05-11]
models/fan holder v2.stl
35.0 x 12.0 x 8.00

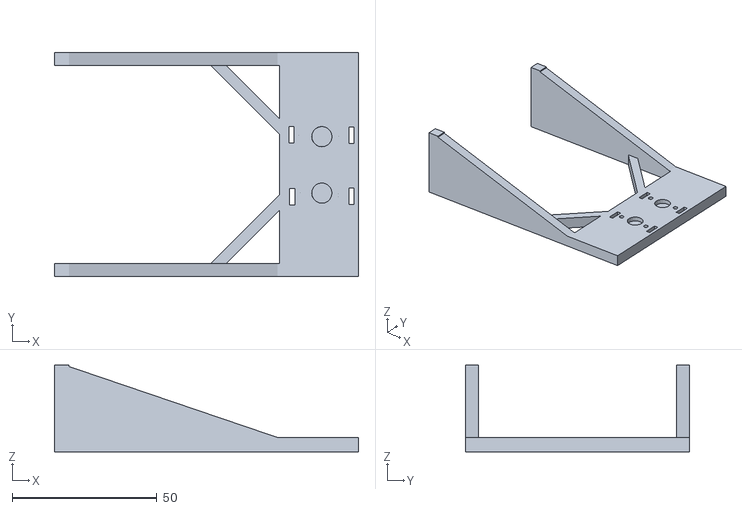
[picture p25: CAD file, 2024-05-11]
models/camera base.stl
105.0 x 77.2 x 30.0

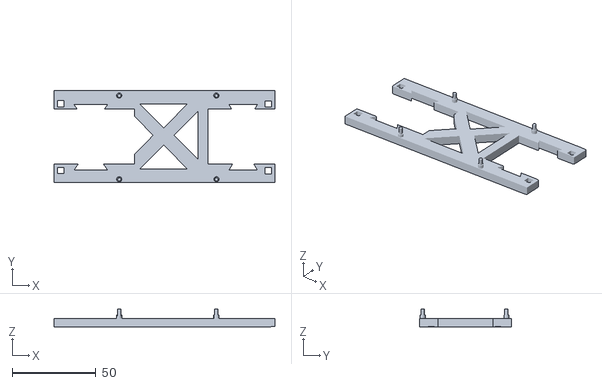
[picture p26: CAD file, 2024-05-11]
models/base test v2.stl
132.0 x 55.0 x 10.5

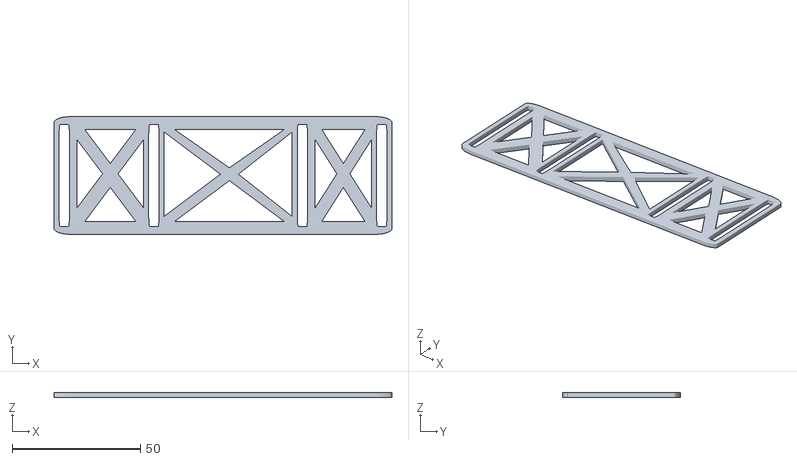
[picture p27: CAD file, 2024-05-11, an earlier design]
models/old/unused/base thing v2.stl
132.0 x 46.0 x 2.00

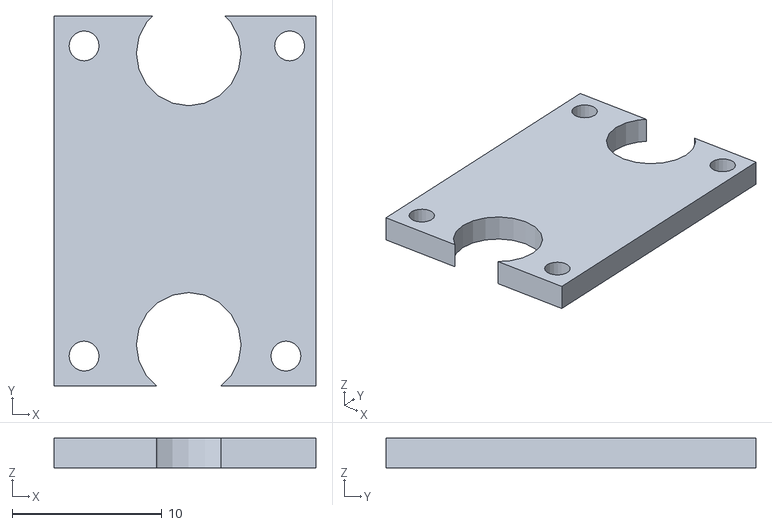
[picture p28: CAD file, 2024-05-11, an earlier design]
models/camera holder v3.stl
17.5 x 24.8 x 2.00

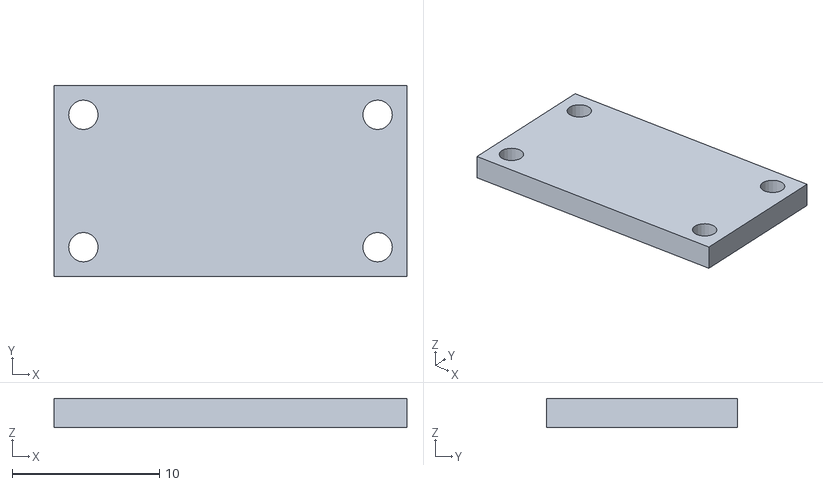
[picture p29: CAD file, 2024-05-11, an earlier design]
models/old/past iterations/camera holder v2.stl
24.0 x 13.0 x 2.00

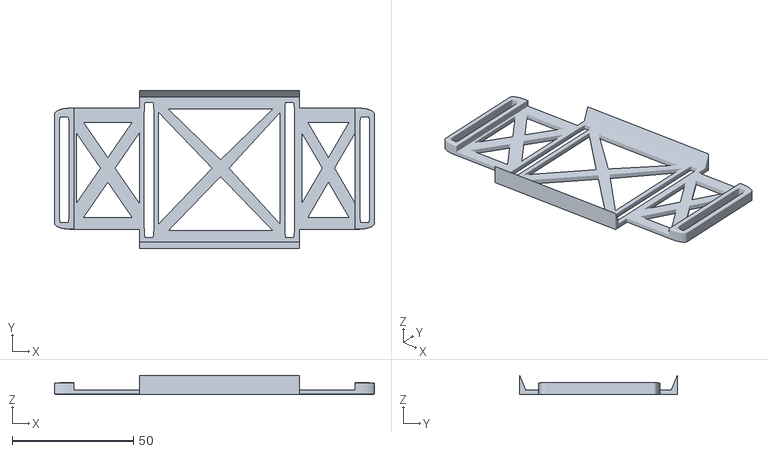
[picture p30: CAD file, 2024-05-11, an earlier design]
models/old/unused/base thing v3.stl
132.0 x 65.0 x 8.00

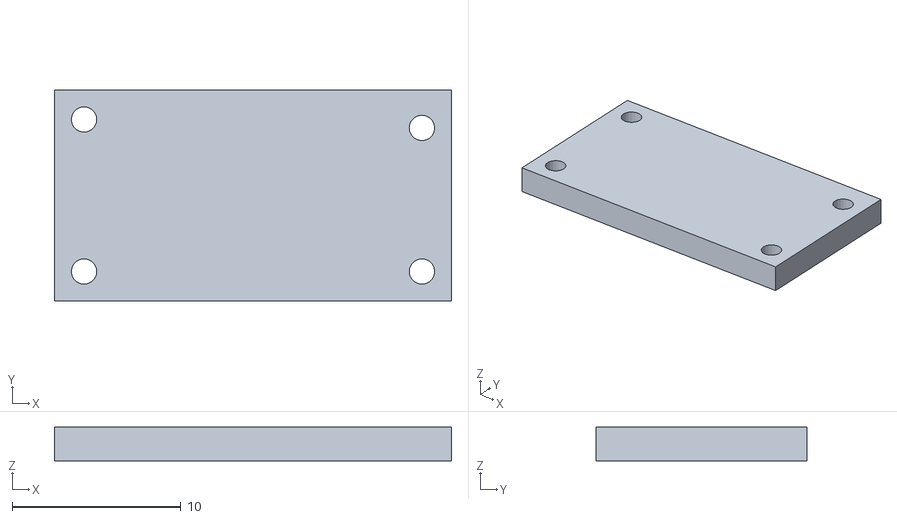
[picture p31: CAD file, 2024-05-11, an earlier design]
models/old/past iterations/camera holder.stl
23.5 x 12.5 x 2.00

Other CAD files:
models/fan hclder v2.stl
models/old/past iterations/fan hclder v2.stl
models/old/past iterations/camera holder v4.stl
models/camera holder v4.stl
models/old/unused/1mm washer.stl
models/old/unused/2mm washer.stl
models/old/unused/3mm washer.stl
models/old/unused/4.mm washer.stl
models/old/unused/base thing v4.stl
models/old/unused/base thing.stl
models/old/unused/washers with cuts.stl

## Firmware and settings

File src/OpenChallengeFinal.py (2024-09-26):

# libraries
import sys
import cv2  # for image processing
import numpy as np  # for image manipulation
import time

sys.path.append(
    "/home/pi/TurboPi/"
)  # navigating to where the raspberry pi libraries are located
from picamera2 import Picamera2
import HiwonderSDK.Board as Board
import RPi.GPIO as GPIO


# movement constants
MID_SERVO = 82
MAX_TURN_DEGREE = 40
DC_SPEED = 1334


# proportion constants for the servo motor angle (PID steering)
PD = 0.2
PG = 0.0035
# no integral value


# ROI constants
ROI_LEFT_BOT = [0, 300, 100, 340]
ROI_RIGHT_BOT = [540, 300, 640, 340]
ROI_LEFT_TOP = [0, 285, 40, 300]
ROI_RIGHT_TOP = [600, 285, 640, 300]
ROI4 = [270, 340, 370, 380]


# color threshold constants (in HSV)
# LOWER_BLUE = np.array([104, 65, 70])
# UPPER_BLUE = np.array([132, 205, 185])
# LOWER_ORANGE1 = np.array([155, 59, 70])
# UPPER_ORANGE1 = np.array([180, 255, 255])
# LOWER_ORANGE2 = np.array([0, 59, 70])
# UPPER_ORANGE2 = np.array([8, 255, 255])

LOWER_ORANGE1 = np.array([180, 100, 100])
UPPER_ORANGE1 = np.array([180, 255, 255])
LOWER_ORANGE2 = np.array([0, 80, 80])
UPPER_ORANGE2 = np.array([20, 255, 255])

LOWER_BLUE = np.array([101, 20, 30])
UPPER_BLUE = np.array([125, 255, 255])

LOWER_BLACK_THRESHOLD = np.array([0, 0, 0])
UPPER_BLACK_THRESHOLD = np.array([180, 255, 80])


# camera settings
WIDTH = 640
HEIGHT = 480
POINTS = [(115, 200), (525, 200), (640, 370), (0, 370)]


# limiting constants
MAX_TURNS = 12
ACTIONS_TO_STRAIGHT = 120
WALL_THRESHOLD = 50
NO_WALL_THRESHOLD = 50
TURN_ITER_LIMIT = 30
LINE_THRESHOLD = 30


# incrementing variables
action_counter = 0
turn_counter = 0
turn_length_counter = 0


# dynamic variables
track_dir = "none"
done_turning = False
turn_dir = "none"
last_difference = 0
current_difference = 0


# initialize servo angle variable
servo_angle = 0


# initialization of camera global variables
im = None
image = None

# activate buzzer, showing that the program has started
Board.setBuzzer(0)  # turn off buzzer
Board.setBuzzer(1)  # turn on buzzer
time.sleep(0.1)
Board.setBuzzer(0)  # turn off buzzer

# wait for button press
key2_pin = 16
GPIO.setmode(GPIO.BOARD)
GPIO.setup(key2_pin, GPIO.IN, pull_up_down=GPIO.PUD_UP)
while GPIO.input(key2_pin) == GPIO.HIGH:
    pass


# camera setup
picam2 = Picamera2()
picam2.preview_configuration.main.size = (640, 480)
picam2.preview_configuration.main.format = "RGB888"
picam2.preview_configuration.controls.FrameRate = 30
picam2.preview_configuration.align()
picam2.configure("preview")
picam2.set_controls(
    {"Saturation": 1.4, "Brightness": 0.05}
)  # adjust brightness and saturation of the image
picam2.start()


# utility function for pwm angle calculation
def pwm(degree):  # angle must be adjusted to pwm angle for servo
    """
    Convert angle in degrees to pulse width modulation (PWM) for servo to understand

    Parameters:
    degree (int): The angle the servo should turn to.

    Returns:
    int: The equivalent pwm for the desired angle.
    """

    return round(degree * 11.1 + 500)


# utility function for drawing ROI
def drawROI(ROI):  # draw the rectangular ROI on the image
    """
    Displays/draws a rectanngular region of interest (ROI) on the OpenCV window

    Parameters:
    ROI (list): A list of 2 coodinates detailing the top left and the bottom right of the ROI

    Returns:

    """

    image = cv2.line(im, (ROI[0], ROI[1]), (ROI[2], ROI[1]), (0, 255, 255), 4)
    image = cv2.line(im, (ROI[0], ROI[1]), (ROI[0], ROI[3]), (0, 255, 255), 4)
    image = cv2.line(im, (ROI[2], ROI[3]), (ROI[2], ROI[1]), (0, 255, 255), 4)
    image = cv2.line(im, (ROI[2], ROI[3]), (ROI[0], ROI[3]), (0, 255, 255), 4)


# utility function for stopping the robot
def stop():
    """
    Sets servo and DC motor straight and closing the OpenCV window

    Parameters:

    Returns:

    """

    time.sleep(0.02)
    Board.setPWMServoPulse(6, 1500, 100)
    Board.setPWMServoPulse(1, pwm(MID_SERVO), 1000)
    time.sleep(0.05)
    Board.setPWMServoPulse(6, 1500, 100)
    cv2.destroyAllWindows()


# setting servo angle to straight and the motor to stationary
Board.setPWMServoPulse(1, pwm(MID_SERVO), 10)  # turn servo to mid
Board.setPWMServoPulse(6, 1500, 100)  # arm the esc motor
time.sleep(0.5)


# main loop
while True:

    # exit if button is pressed
    if GPIO.input(key2_pin) != GPIO.HIGH:
        stop()
        break

    # setup camera frame
    im = picam2.capture_array()
    input = np.float32(POINTS)
    output = np.float32(
        [(0, 0), (WIDTH - 1, 0), (WIDTH - 1, HEIGHT - 1), (0, HEIGHT - 1)]
    )

    # convert to hsv
    img_hsv = cv2.cvtColor(im, cv2.COLOR_BGR2HSV)

    # find black thresholds/mask and store them in a variable
    img_thresh = cv2.inRange(img_hsv, LOWER_BLACK_THRESHOLD, UPPER_BLACK_THRESHOLD)

    # find black contours in left and right regions
    left_contours_top, hierarchy = cv2.findContours(
        img_thresh[
            ROI_LEFT_TOP[1] : ROI_LEFT_TOP[3], ROI_LEFT_TOP[0] : ROI_LEFT_TOP[2]
        ],
        cv2.RETR_EXTERNAL,
        cv2.CHAIN_APPROX_NONE,
    )
    right_contours_top, hierarchy = cv2.findContours(
        img_thresh[
            ROI_RIGHT_TOP[1] : ROI_RIGHT_TOP[3], ROI_RIGHT_TOP[0] : ROI_RIGHT_TOP[2]
        ],
        cv2.RETR_EXTERNAL,
        cv2.CHAIN_APPROX_NONE,
    )
    left_contours_bot, hierarchy = cv2.findContours(
        img_thresh[
            ROI_LEFT_BOT[1] : ROI_LEFT_BOT[3], ROI_LEFT_BOT[0] : ROI_LEFT_BOT[2]
        ],
        cv2.RETR_EXTERNAL,
        cv2.CHAIN_APPROX_NONE,
    )
    right_contours_bot, hierarchy = cv2.findContours(
        img_thresh[
            ROI_RIGHT_BOT[1] : ROI_RIGHT_BOT[3], ROI_RIGHT_BOT[0] : ROI_RIGHT_BOT[2]
        ],
        cv2.RETR_EXTERNAL,
        cv2.CHAIN_APPROX_NONE,
    )

    # define variables for left and right ROI contour areas
    left_area_top = 0
    left_area_bot = 0

    right_area_top = 0
    right_area_bot = 0

    # loop to find largest contours
    for i in range(len(left_contours_top)):
        cnt = left_contours_top[i]
        area = cv2.contourArea(cnt)
        left_area_top = max(area, left_area_top)
    for i in range(len(left_contours_bot)):
        cnt = left_contours_bot[i]
        area = cv2.contourArea(cnt)
        left_area_bot = max(area, left_area_bot)
    for i in range(len(right_contours_top)):
        cnt = right_contours_top[i]
        area = cv2.contourArea(cnt)
        right_area_top = max(area, right_area_top)
    for i in range(len(right_contours_bot)):
        cnt = right_contours_bot[i]
        area = cv2.contourArea(cnt)
        right_area_bot = max(area, right_area_bot)

    # combine areas on each side
    right_area = right_area_bot + right_area_top
    left_area = left_area_bot + left_area_top

    # find blue thresholds/mask and store them in a variable
    b_mask = cv2.inRange(img_hsv, LOWER_BLUE, UPPER_BLUE)

    # find blue contours to detect the lines on the mat
    contours_blue = cv2.findContours(
        b_mask[ROI4[1] : ROI4[3], ROI4[0] : ROI4[2]],
        cv2.RETR_EXTERNAL,
        cv2.CHAIN_APPROX_SIMPLE,
    )[-2]

    # find orange thresholds/mask and store them in a variable
    o_mask = cv2.bitwise_or(
        cv2.inRange(img_hsv, LOWER_ORANGE1, UPPER_ORANGE1),
        cv2.inRange(img_hsv, LOWER_ORANGE2, UPPER_ORANGE2),
    )

    # find orange contours to detect the lines on the mat
    contours_orange = cv2.findContours(
        o_mask[ROI4[1] : ROI4[3], ROI4[0] : ROI4[2]],
        cv2.RETR_EXTERNAL,
        cv2.CHAIN_APPROX_SIMPLE,
    )[-2]

    # iterate through the blue and orange contours and store the maximum area
    max_blue_area = 0
    max_orange_area = 0

    for i in range(len(contours_orange)):
        cnt = contours_orange[i]
        max_orange_area = max(cv2.contourArea(cnt), max_orange_area)
        cnt[:, :, 0] += ROI4[0]  # Add X offset
        cnt[:, :, 1] += ROI4[1]  # Add Y offset
        cv2.drawContours(
            im, contours_orange, i, (255, 255, 0), 1
        )  # draw the contours for debug utility
    for i in range(len(contours_blue)):
        cnt = contours_blue[i]
        max_blue_area = max(cv2.contourArea(cnt), max_blue_area)
        cnt[:, :, 0] += ROI4[0]  # Add X offset
        cnt[:, :, 1] += ROI4[1]  # Add Y offset
        cv2.drawContours(
            im, contours_blue, i, (255, 255, 0), 1
        )  # draw the contours for debug utility
    if track_dir == "none":  # find which direction the track is going
        if (
            max_blue_area > max_orange_area and max_blue_area > LINE_THRESHOLD
        ):  # if blue is first seen, the track direction is left (counter clockwise)
            track_dir = "left"
        if (
            max_orange_area > max_blue_area and max_orange_area > LINE_THRESHOLD
        ):  # if orange is first seen, the track direction is right (clockwise)
            track_dir = "right"
    if track_dir == "right":
        if (
            turn_dir
            == "right"  # if the robot is in a sharp turn but sees the opposite colour, the turn is stopped
            and max_blue_area > LINE_THRESHOLD
            and max_orange_area < LINE_THRESHOLD
        ):
            done_turning = True
            turn_dir = "none"
        elif max_orange_area > LINE_THRESHOLD:  # signals that a turn must occur
            # if the turn direction hasn't been changed yet change the turn direction to right

            if turn_dir == "none":
                turn_counter += 1
                turn_dir = "right"
    elif track_dir == "left":
        if (
            turn_dir
            == "left"  # if the robot is in a sharp turn but sees the opposite colour, the turn is stopped
            and max_orange_area > LINE_THRESHOLD
            and max_blue_area < LINE_THRESHOLD
        ):
            done_turning = True
            turn_dir = "none"
        elif max_blue_area > LINE_THRESHOLD:  # signals that a turn must occur
            # if the turn direction hasn't been changed yet change the turn direction to left

            if turn_dir == "none":
                turn_counter += 1
                turn_dir = "left"
    if (
        done_turning
    ):  # if the robot has just completed a turn, make it continue the turn to assure that it sees the two parallel walls
        turn_length_counter += 1

        if (
            turn_length_counter > TURN_ITER_LIMIT
        ):  # turn for the required amount of time
            turn_length_counter = 0
            done_turning = False
    else:

        if turn_dir == "right":  # calculate the servo angle for the current turn
            servo_angle = MID_SERVO - MAX_TURN_DEGREE
        elif turn_dir == "left":  # calculate the servo angle for the current turn
            servo_angle = MID_SERVO + MAX_TURN_DEGREE
        else:
            turn_length_counter = 0  # reset the turn length counter
            if (
                left_area < WALL_THRESHOLD
            ):  # if the left area is below the threshold, set the servo angle to max for a sharp left turn
                servo_angle = MID_SERVO + MAX_TURN_DEGREE
            elif (
                right_area < WALL_THRESHOLD
            ):  # if the right area is below the threshold, set the servo angle to max for a sharp right turn
                servo_angle = MID_SERVO - MAX_TURN_DEGREE
            else:
                # if in the straight section, calculate the current_difference between the contours in the left and right area

                current_difference = left_area - right_area

                # calculate steering amount using preportional-derivative steering
                # multiply the current_difference by a constant variable and add the projected error multiplied by another constant
                # this method gives stable and smooth steering

                servo_angle = MID_SERVO - (
                    current_difference * PG
                    + (current_difference - last_difference) * PD
                )
    if (
        turn_counter == MAX_TURNS and not done_turning
    ):  # if the total turns has surpassed the amount required, increment the action counter by 1
        action_counter += 1  # this is to ensure that the robot stops in the middle of the straight section

    # set the last current_difference equal to the current current_difference for derivative steering
    last_difference = current_difference

    # if the steering variable is higher than the max turn degree for the servo, set it to the max turn degree
    # move the motors using the variables
    pw = pwm(servo_angle)
    Board.setPWMServoPulse(6, DC_SPEED, 100)
    Board.setPWMServoPulse(1, pw, 1000)

    # draw the ROIs
    drawROI(ROI_LEFT_TOP)
    drawROI(ROI_RIGHT_TOP)
    drawROI(ROI_LEFT_BOT)
    drawROI(ROI_RIGHT_BOT)
    drawROI(ROI4)

    # display the camera
    if len(sys.argv) > 1 and sys.argv[1] == "Debug":
        cv2.imshow("Camera", im)

    # if the number of actions to the straight section has been met, stop the car
    if cv2.waitKey(1) == ord("q") or action_counter >= ACTIONS_TO_STRAIGHT:
        stop()
        break

cv2.destroyAllWindows()

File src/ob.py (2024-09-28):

# libraries
import math
import sys
import cv2  # for image processing
import numpy as np  # for image manipulation
import time

sys.path.append("/home/pi/TurboPi/")
from picamera2 import Picamera2
import HiwonderSDK.Board as Board
import libcamera  # for adjusting camera settings
from libcamera import controls
import RPi.GPIO as GPIO


# ROIs (region of interest)

ROI_LEFT_BOT = [0, 290, 220, 420]
ROI_RIGHT_BOT = [420, 290, 640, 420]
ROI_LEFT_TOP = [0, 260, 50, 290]
ROI_RIGHT_TOP = [590, 260, 640, 290]
ROI4 = [120, 320, 520, 340]
ROI_MIDDLE = [0, 210, 640, 420]
ROI_PARKING_LEFT = [0, 225, 320, 445]
ROI_PARKING_RIGHT = [320, 225, 640, 445]
ROI_FRONT = [285, 320, 355, 350]

# proportion constants for the servo motor angle (PD steering) for the wall following algorithm

PD = 0.03
PG = 0.0017
# camera constants

WIDTH = 640
HEIGHT = 480
POINTS = [(115, 200), (525, 200), (640, 370), (0, 370)]

# colour thresholds


LOWER_BLACK_THRESHOLD = np.array([0, 0, 0])
UPPER_BLACK_THRESHOLD = np.array([180, 255, 57])
"""

LOWER_RED_THRESHOLD1 = np.array([4, 134, 80])
UPPER_RED_THRESHOLD1 = np.array([12, 255, 255])
LOWER_RED_THRESHOLD2 = np.array([180, 144, 107])
UPPER_RED_THRESHOLD2 = np.array([180, 255, 255])

LOWER_GREEN_THRESHOLD = np.array([45, 87, 50])
UPPER_GREEN_THRESHOLD = np.array([80, 255, 175])

LOWER_ORANGE_THRESHOLD1 = np.array([180, 100, 100])
UPPER_ORANGE_THRESHOLD1 = np.array([180, 255, 255])
LOWER_ORANGE_THRESHOLD2 = np.array([17, 175, 150])
UPPER_ORANGE_THRESHOLD2 = np.array([26, 255, 240])

LOWER_BLUE_THRESHOLD = np.array([29, 0, 50])
UPPER_BLUE_THRESHOLD = np.array([110, 100, 115])

LOWER_MAGENTA_THRESHOLD1 = np.array([0, 100, 50])
UPPER_MAGENTA_THRESHOLD1 = np.array([2, 215, 255])

LOWER_MAGENTA_THRESHOLD2 = np.array([166, 110, 50])
UPPER_MAGENTA_THRESHOLD2 = np.array([180, 255, 255])

"""

LOWER_RED_THRESHOLD1 = np.array([0, 154, 80])
UPPER_RED_THRESHOLD1 = np.array([0, 255, 255])
LOWER_RED_THRESHOLD2 = np.array([164, 180, 107])
UPPER_RED_THRESHOLD2 = np.array([180, 255, 255])

LOWER_GREEN_THRESHOLD = np.array([65, 85, 60])
UPPER_GREEN_THRESHOLD = np.array([105, 255, 185])

LOWER_ORANGE_THRESHOLD1 = np.array([180, 80, 80])
UPPER_ORANGE_THRESHOLD1 = np.array([180, 255, 255])
LOWER_ORANGE_THRESHOLD2 = np.array([0, 80, 100])
UPPER_ORANGE_THRESHOLD2 = np.array([20, 255, 255])

LOWER_BLUE_THRESHOLD = np.array([110, 30, 40])
UPPER_BLUE_THRESHOLD = np.array([130, 250, 140])

LOWER_MAGENTA_THRESHOLD1 = np.array([0, 100, 50])
UPPER_MAGENTA_THRESHOLD1 = np.array([0, 215, 255])

LOWER_MAGENTA_THRESHOLD2 = np.array([150, 150, 100])
UPPER_MAGENTA_THRESHOLD2 = np.array([161, 255, 255])


LINE_THRESHOLD = 80  # minimum contour size of orange or blue line

PILLAR_SIZE = 350  # pillar size constant


# motor constants

DC_SPEED = 1342
MID_SERVO = 82
MAX_TURN_DEGREE = 42

ACTIONS_TO_STRAIGHT = (
    140  # number of iterations to enter the straight section from the turning section
)

action_counter = 50  # counter to determine when the robot has entered the straight section from the turning section

# pillar avoidance algorithm variables

prevPillar = ""  # keeps track of previous pillar
target = None
pillar_error = 0
prev_pillar_error = 0
red_target = 110
green_target = 530


# variables used for last lap

tpt_no_red = False  # keep track of whether there is a red pillar to decide when to initiate the three point turn
tpt_two_red = False  # signal that there was two red pillars after the last turn
need_space = False  # keep track of whether there is enough space to initiate the three point turn
lastLapTurnAround = False  # if the last lap is the opposite direction
lastLapContinue = False  # if the last lap is the same direction

# variables for turning algorithm

total_turn = 0  # incrementing variable for the total number of turns
turnDir = None  # keeps track of the current turn direction
trackDir = None  # keeps track of the current track direction
line_seen = False  # keeps track of whether the line has been seen
threeLaps = False  # used to determine when the robot has completed 3 laps and can stop
# turnIter = 0
# turnIterLimit = 10
# wall following variables
last_difference = 0  # used for derivative calculation for wall following
current_difference = 0  # used for derivative calculation for wall following

# variables used for parking
need_pause = True
parkingR = False
parkingL = False
parking_algorithm = False

servo_angle = 0  # current servo angle


Board.setBuzzer(0)  # turn off buzzer
Board.setBuzzer(1)  # turn on buzzer
time.sleep(0.1)
Board.setBuzzer(0)  # turn off buzzer

# wait for button press

key2_pin = 16
GPIO.setmode(GPIO.BOARD)
GPIO.setup(key2_pin, GPIO.IN, pull_up_down=GPIO.PUD_UP)
"""
while GPIO.input(key2_pin) == GPIO.HIGH:
    pass
"""


# camera setup
picam2 = Picamera2()
picam2.preview_configuration.main.size = (640, 480)
picam2.preview_configuration.main.format = "RGB888"
picam2.preview_configuration.controls.FrameRate = 30
picam2.preview_configuration.align()

"""
picam2.set_controls(
    {
        "Brightness": 0.05,  # adjust brightness
        "AwbMode": libcamera.controls.AwbModeEnum.Custom,  # adjust red and blue gains
        "ColourGains": (1.08, 1),
    }
)
"""


picam2.configure("preview")


picam2.start()  # start the camera


def drawROI(ROI):  # draw the rectangular ROI on the image
    """
    Displays/draws a rectanngular region of interest (ROI) on the OpenCV window

    Parameters:
    ROI (list): A list of 2 coodinates detailing the top left and the bottom right of the ROI

    Returns:

    """

    image = cv2.line(im, (ROI[0], ROI[1]), (ROI[2], ROI[1]), (0, 255, 255), 4)
    image = cv2.line(im, (ROI[0], ROI[1]), (ROI[0], ROI[3]), (0, 255, 255), 4)
    image = cv2.line(im, (ROI[2], ROI[3]), (ROI[2], ROI[1]), (0, 255, 255), 4)
    image = cv2.line(im, (ROI[2], ROI[3]), (ROI[0], ROI[3]), (0, 255, 255), 4)


# utility function for pwm angle calculation
def pwm(degree):
    """
    Convert angle in degrees to pulse width modulation (PWM) for servo to understand

    Parameters:
    degree (int): The angle the servo should turn to.

    Returns:
    int: The equivalent pwm for the desired angle.
    """
    return round(degree * 11.1 + 500)


def stop():
    """
    Sets servo and DC motor straight and closing the OpenCV window

    Parameters:

    Returns:

    """
    Board.setPWMServoPulse(6, 1500, 100)
    Board.setPWMServoPulse(1, pwm(MID_SERVO), 1000)
    Board.setPWMServoPulse(6, 1500, 100)
    cv2.destroyAllWindows()
    sys.exit()
    return 0


def findMaxContour(contours):
    """
    Find the largest contour in a list of contours

    Parameters:
    contours (list): A list of contours

    Returns:
    max_area (int): The area of the largest contour
    """

    max_area = 0
    for i in range(len(contours)):

        area = cv2.contourArea(contours[i])
        max_area = max(area, max_area)
    return max_area
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

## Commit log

2024-05-10 Fine-tuned movement and image processing
    - Reverted to the original steering variable
    - Changed black threshold
    - Counted amount of sharp turns
    - Added variable to count iterations
    - Fine-tuned movement
    - Changed straight section speed and turning speed
2024-05-11 Added comments, changed variable names to be standard, changed formatting, cleaned code up
    - standardized variable names, dividing them into constants and dynamic variables
    - added comments for clarity
    - fixed a bug preventing the dc motor turn speed from being used
    - removed the unnecessary "no walls" condition
    - made many new constants
    - combined the two ways for the car to stop into one condition
2024-05-12 Updated PI expansion board
2024-06-23 added schematic
2024-06-27 reorgaizinng models
    [1mm washer.stl, 2mm washer.stl, 3mm washer.stl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]
2024-08-25 Finalize open challenge algorithm
    Added small timer after blue/orange line detected to allow for the wall to fully disappear.
2024-08-25 Fixed variable formatting and added comments
    Not finished full commenting
    [OpenChallengeFinal.py]
2024-08-28 expansion board pictures/diagrams
2024-08-28 expansion and pi schematics
2024-08-28 zip models
    [1mm washer.stl, 2mm washer.stl, 3mm washer.stl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]
2024-08-28 engineering material images
2024-08-28 engineering materials images
2024-08-28 schematic images
2024-08-31 Rename Full Vehicle Schematic.png to Vehicle Schematic.png
2024-09-02 Update and rename camera holder v5.gcode to camera base.gcode
2024-09-02 Rename camera holder v5.stl to camera base.stl
    [camera base.stl]
2024-09-02 unzipped old models
    [1mm washer.stl, 2mm washer.stl, 3mm washer.stl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]
2024-09-03 Fine-tune open challenge variables and algorithms
    Parking algorithm changed to park earlier
    Fixed errors
    [ObstacleChallenge.py]
2024-09-22 steering materials added
2024-09-24 new steering area material
2024-09-28 Finalize Obstacle Challenge for International Competition
    Change turning algorithm, turning ROI.
    Turning algorithm:
    - changed to seperate pillar turn and non-pillar turn
    - if pillar is detected, end turn when pillar is on the correct side of the screen
    - if pillar is not detected, end turn when opposite coloured line is seen as well as the opposite wall
    Added front ROI to detect wall in front of robot
    Altered parking algorithm
    Changed obstacle detection and avoidance
    [ob.py]
